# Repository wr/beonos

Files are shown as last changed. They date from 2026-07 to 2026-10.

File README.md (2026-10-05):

<p align="center">
  Beonos logo
</p>
<h1 align="center">Beonos Controller</h1>

<p align="center">
  <strong>Control your vintage Bang & Olufsen Beogram turntable from Home Assistant or Sonos.</strong>
</p>

<p align="center">
  <a href="#what-is-it">What is it?</a> ⬪
  <a href="#buy-a-board">Buy a board</a> ⬪
  <a href="#which-turntables">Which turntables</a> ⬪
  <a href="#hardware">Hardware</a> ⬪
  <a href="#firmware-esphome">Firmware</a> ⬪
  <a href="#repo-layout">Repo layout</a> ⬪
  <a href="#license">License</a>
</p>

<p align="center">
  <a href="https://youtu.be/ydfJdppEwTE">YouTube player</a>
</p>

<p align="center">
  I recorded a full build video that <a href="https://youtu.be/ydfJdppEwTE">you can watch here</a>.
</p>

---

## Buy a board

Get it as a kit, pre-soldered or not, from the [Wells Workshop shop](https://shop.wells.ee/products/beonos-kit/?ref=gh-beonos).

Or order your own Beonos Controller from [PCBway](https://www.pcbway.com/project/shareproject/Beonos_Controller_80184a3d.html). You can [use my referral code](https://pcbway.com/g/AsfKU9) to get $5 off your order, if you want. In my experience they're usually pretty fast and high quality, especially for the price.

## What is it?

A small ESP32-C6-powered custom PCB that splices into a Beogram's keyboard cable, reads what the turntable is doing, and sends play/pause/stop commands. The result is a 'smart' vintage turntable that behaves like a digital Sonos source.

- **Turntable → Sonos**: start the turntable and the speaker switches to Line-In and plays. Pause or switch off, and the speaker pauses.
- **Sonos → turntable**: pick Line-In on the speaker and the turntable starts (it presses Cue). Switch away or pause, and the turntable stops. If there's no record on the platter, the firmware notices and pauses Sonos rather than leaving it playing silence.

The board splices in-line, so nothing about the turntable is modified permanently — unplug the two headers and it's stock again.

## Which turntables

The Beogram 1800 family — the last generation of radial-arm Beograms — all share one control board, so the splice is the same across them:

| Model | Years | Status |
| ----- | ----- | --- |
| Beogram RX 2 | 1985–90 | Built and tested against this |
| Beogram 1800 | 1983–84 | Confirmed from service manuals |
| Beogram 2000 | 1983 | Confirmed from service manuals |
| Beogram 5000 | 1984 | Confirmed from service manuals |
| Beogram RX | 1984 | Very likely, not yet verified |

The RX-2 service manual is published as a supplement to the Beogram 1800/2000/5000 manual, and the three share the same power supply (PCB 8005076) and control board (PCB 8005117). Their keyboards are the same two sub-boards — 8005070 for PLAY/STOP and 8005109 for 45/CUE/33 — landing on the same P7 pins, which is what this board splices into. The RX is unverified only because no manual was to hand; it replaced the 1800 and differs from the RX 2 mainly in being supplied with a pickup.

**Not compatible.** The Beogram 2200 looks close but wires its speed switches straight to the control board alongside indicator lamps and a motor relay, with no separate keyboard board and no CUE or PLAY/STOP lines to intercept. Tangential-arm Beograms (4002, 8000, 6500, 7000, 9000, 5005 and relatives) use a different arm and control system entirely, and pre-1983 radial decks predate this microcomputer control.

To identify an unknown deck, look for a control PCB stamped **8005117**, a 24-pin MCU marked **B040680** / **ETL 5410N**, and a keyboard on its own cable whose buttons switch +12V.

## Hardware

- **MCU**: Seeed Studio XIAO ESP32-C6 (castellated edge-mount module)
- **Button drivers**: 2× LTV-356T optocouplers, switching the turntable's +12V onto the CUE and PLAYPAUSE lines exactly as the real buttons do
- **Level shifters**: 2× 1M/1.5M dividers dropping the COP410's 5.3V logic to ~3.18V for the ESP's 3.3V inputs. The values are deliberately high so the divider barely loads the COP410's weak CMOS outputs, and any overvoltage is current-limited into the ESP's ESD clamps.
- **Power**: an off-board MP1584EN buck module (PS1) steps the +12V button rail down to 5V, so the board draws everything from the button cable and never taps the 5.3V supply. The module hangs on flying leads; the board carries four wire pads for it.
- **Decoupling**: 10µF + 100nF on the buck's 5V output
- **Input filtering**: 10nF from each divider midpoint to ground, below R6/R8. The dividers present ~600kΩ to the ESP on wires that run past a motor; the caps give a ~6ms time constant, well inside the firmware's 50 ms debounce.
- **Connectors**: two 1×8 horizontal headers for the in-line splice — J1 (socket, silkscreened `TO BOARD`) and J2 (header, silkscreened `TO KEYBOARD`). Pins 1, 2, 4, 6, 7, 8 pass straight through; pins 3 and 5 also land on the optocoupler emitters.
- **Flying leads**: the two COP410 sense signals and a ground reference arrive on test pads (TP2, TP3, TP5); four more pads go out to the buck module. Everything is silkscreened by function — `On-Off IN`, `PlayPause IN`, `GND IN`, `12V`, `5V`, `GND` — so solder by the printed label, not the designator.

Board is 25 × 64 mm, two layers. Sources are `beogram-esp32.kicad_pcb` / `.kicad_sch` / `.kicad_pro`, with the BOM in [`bom.csv`](bom.csv).

### Pin map

| XIAO pin | Pad | GPIO | Net | Purpose |
| --- | --- | --- | --- | --- |
| D0 | 1 | GPIO0  | IN_OnOff_3V3 | COP410 pin 11 → ESP. LOW = arm in (turntable on) |
| D3 | 4 | GPIO21 | IN_PlayPause_3V3  | COP410 pin 12 → ESP. HIGH = playing |
| D8 | 9 | GPIO19 | DRV_PlayPause | ESP → U2 opto LED. Pulse 500 ms to "press" PLAYPAUSE |
| D10 | 11  | GPIO18 | DRV_Cue | ESP → U3 opto LED. Pulse 500 ms to "press" CUE |
| 5V | 14  | — | VCC | 5V in from the MP1584 buck (PS1) |
| GND | 13  | — | GND | Common ground |

D6/D7 (GPIO16/17) are UART0 and are left unconnected on purpose, so the ROM bootloader's serial output can't reach an optocoupler on reset.

## Firmware (ESPHome)

```bash
pip install esphome
cp secrets.yaml.example secrets.yaml
# fill in WiFi creds in secrets.yaml
esphome run beogram-rx2.yaml
```

First flash needs USB-C; after that, updates go over the air.

### Configuring the Sonos speaker

Once it joins WiFi the device shows up in Home Assistant. Set the **"Sonos IP"** entity to your speaker's address. That's the only setup — the RINCON UUID is discovered from the speaker on boot.

### Exposed entities

| Entity | Type | Notes |
| --- | --- | --- |
| Turntable On | binary_sensor  | true = arm in / playing position |
| Turntable Playing | binary_sensor  | true = motor on, arm down |
| Sonos Playing | binary_sensor  | derived from polled transport state |
| Sonos On Line-In | binary_sensor  | true if speaker is on line-in |
| Sonos Transport State | text_sensor | PLAYING / PAUSED_PLAYBACK / STOPPED |
| Sonos Current URI | text_sensor | what the speaker is currently playing |
| Sonos IP | text (config)  | edit in HA, persists across reboots |
| Press Play/Pause | button | manually fire the turntable's PLAYPAUSE |
| Press Cue | button | manually fire the turntable's CUE |
| Sonos Play / Pause | buttons | manual SOAP commands |
| Sonos Switch to Line-In | button | manual SOAP command |
| WiFi Signal | sensor | dBm, 60s update |

## Repo layout

```
beogram-esp32.kicad_pro     KiCad project
beogram-esp32.kicad_sch     Schematic
beogram-esp32.kicad_pcb     PCB layout
fp-lib-table                Registers the project footprint libraries
sym-lib-table               Registers the project symbol library
beogram.pretty/             Project footprints (MP1584 wire pads)
beogram.kicad_sym           Project symbols
New_XIAO_Series_Footprints/ Seeed's XIAO footprint library (vendor)
beogram-rx2.yaml            ESPHome firmware config
secrets.yaml.example        Template for WiFi/OTA/API creds
bom.csv                     Bill of materials
bang-olufsen_beogram_rx2_sch.pdf   RX 2 service-manual schematic, for reference
```

## Credits

ESPHome, the Seeed Studio XIAO ESP32-C6, KiCad, and Bang & Olufsen's engineers, who documented the RX2 well enough to reverse a splice point out of it forty years later.

## Donate

While beonos is free and open source, donations are deeply appreciated, and make ongoing development and support possible.
[Donate now](https://www.buymeacoffee.com/wellsworkshop)

## License

[CC BY-NC-SA 4.0](LICENSE). © 2026 Wells Riley.

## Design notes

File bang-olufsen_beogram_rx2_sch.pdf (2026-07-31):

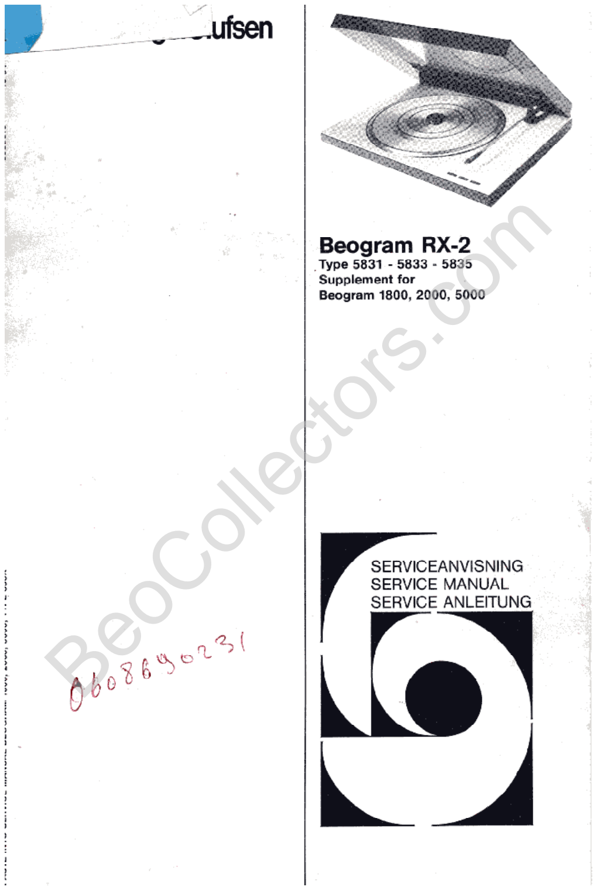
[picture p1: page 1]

BeoCollectors.

com

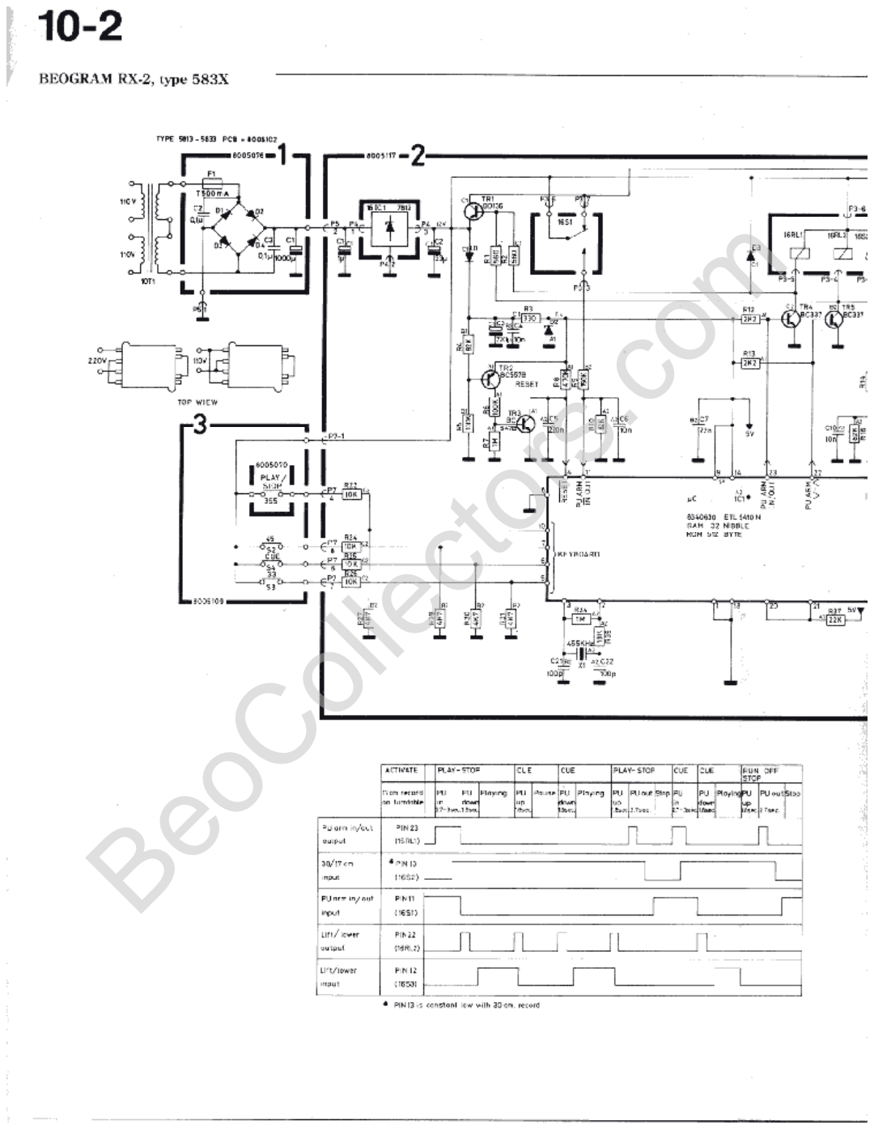
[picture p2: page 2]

BeoCollectors.

com

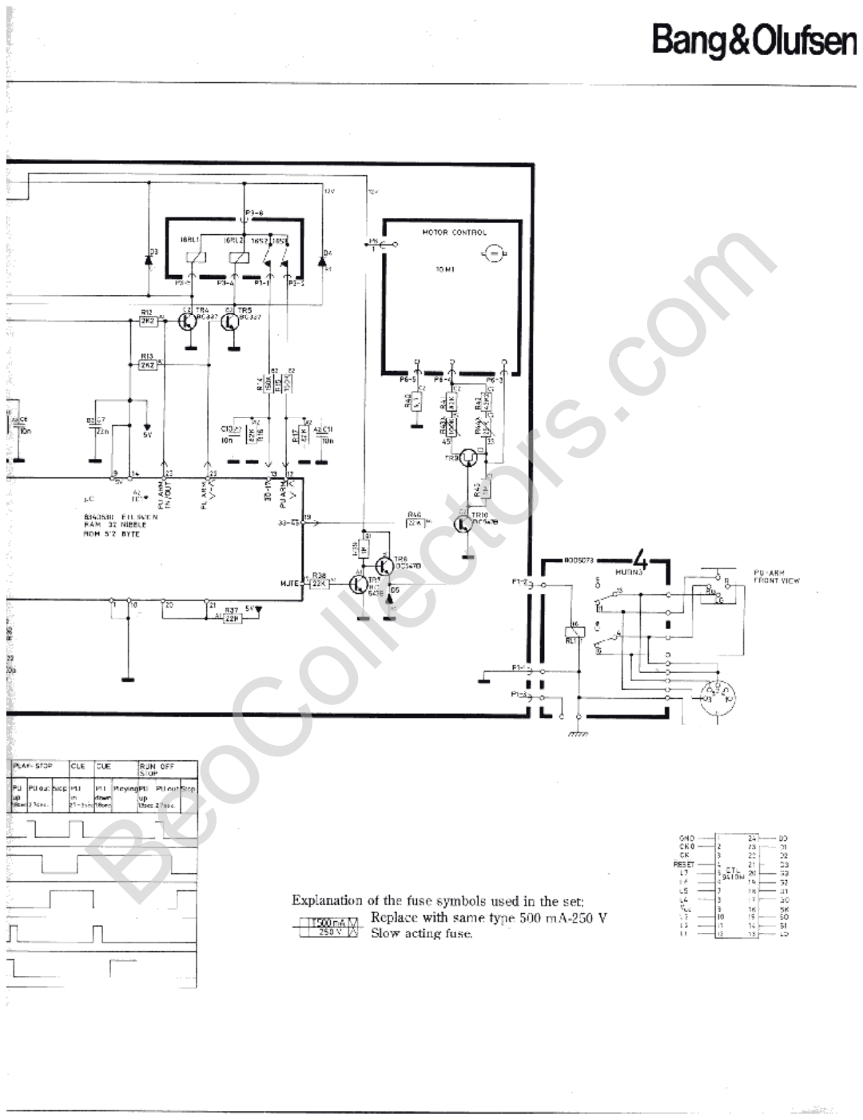
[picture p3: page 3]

BeoCollectors.

com

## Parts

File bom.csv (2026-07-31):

references | value | footprint | quantity
C2 | 100nF | Capacitor_SMD:C_0402_1005Metric | 1
C3,C4 | 10nF | Capacitor_SMD:C_0402_1005Metric | 2
C1 | 10uF | Capacitor_SMD:C_0402_1005Metric | 1
J2 | 2.54-1*40P right-angle(C2334) | Connector_PinHeader_2.54mm:PinHeader_1x08_P2.54mm_Horizontal | 1
J1 | PM254-1-08-W-8.5(C2897390) | Connector_PinSocket_2.54mm:PinSocket_1x08_P2.54mm_Horizontal | 1
U1 | SEEED STUDIO XIAO ESP32C6 | New_XIAO_Series_Footprints:XIAO-ESP32-C6-SMD | 1
U2,U3 | LTV-356T | Package_SO:SO-4_4.4x3.6mm_P2.54mm | 2
R6,R8 | 1.5M | Resistor_SMD:R_0402_1005Metric | 2
R5,R7 | 1M | Resistor_SMD:R_0402_1005Metric | 2
R1,R2 | 470R | Resistor_SMD:R_0402_1005Metric | 2
PS1 | MP1584EN module | beogram:MP1584_Module_Wired | 1

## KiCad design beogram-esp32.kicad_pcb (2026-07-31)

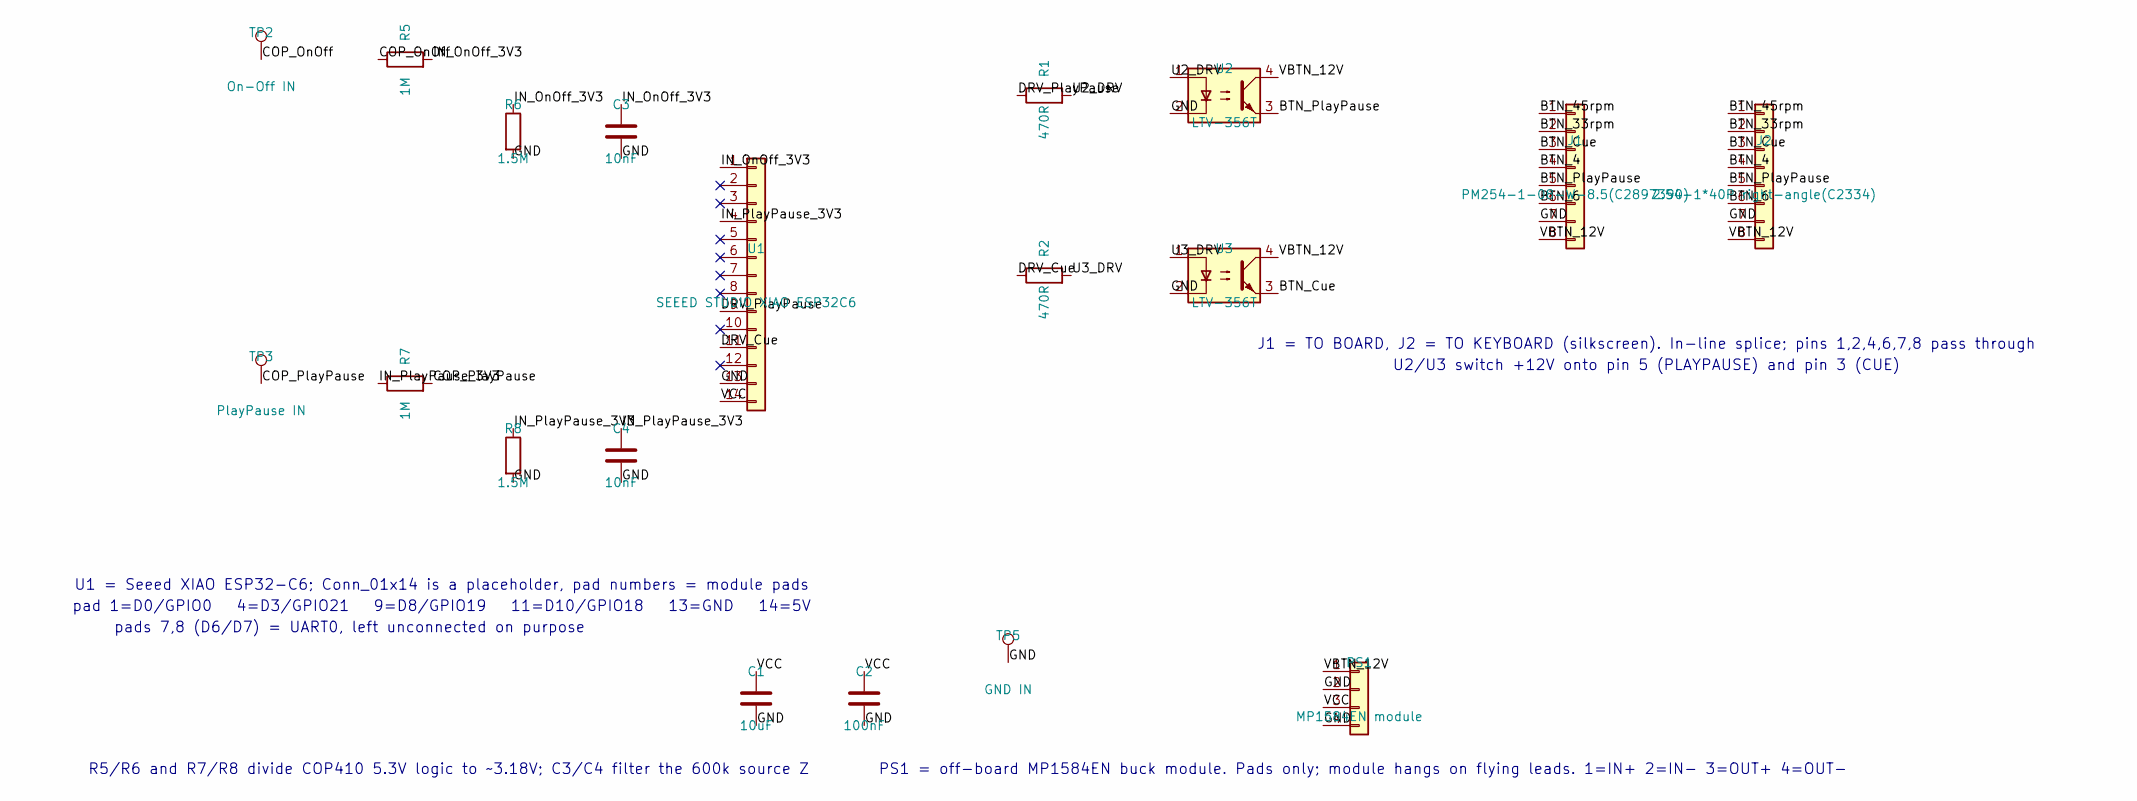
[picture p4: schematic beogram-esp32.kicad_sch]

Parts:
C1: 10uF; C_0402_1005Metric
C2: 100nF; C_0402_1005Metric
C3, C4: 10nF; C_0402_1005Metric
J1: PM254-1-08-W-8.5(C2897390); PinSocket_1x08_P2.54mm_Horizontal
J2: 2.54-1*40P right-angle(C2334); PinHeader_1x08_P2.54mm_Horizontal
PS1: MP1584EN module; MP1584_Module_Wired
R1, R2: 470R; R_0402_1005Metric
R5, R7: 1M; R_0402_1005Metric
R6, R8: 1.5M; R_0402_1005Metric
TP2: On-Off IN; TestPoint_Pad_1.5x1.5mm
TP3: PlayPause IN; TestPoint_Pad_1.5x1.5mm
TP5: GND IN; TestPoint_Pad_1.5x1.5mm
U1: SEEED STUDIO XIAO ESP32C6; XIAO-ESP32-C6-SMD
U2, U3: LTV-356T; SO-4_4.4x3.6mm_P2.54mm

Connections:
BTN_4: J1.4, J2.4
BTN_6: J1.6, J2.6
BTN_33rpm: J1.2, J2.2
BTN_45rpm: J1.1, J2.1
BTN_Cue: J1.3, J2.3, U3.3
BTN_PlayPause: J1.5, J2.5, U2.3
COP_OnOff: R5.1, TP2.1
COP_PlayPause: R7.2, TP3.1
DRV_Cue: R2.1, U1.11
DRV_PlayPause: R1.1, U1.9
GND: C1.2, C2.1, C3.1, C4.2, J1.7, J2.7, PS1.2, PS1.4, R6.2, R8.2, TP5.1, U1.13, U2.2, U3.2
IN_OnOff_3V3: C3.2, R5.2, R6.1, U1.1
IN_PlayPause_3V3: C4.1, R7.1, R8.1, U1.4
U2_DRV: R1.2, U2.1
U3_DRV: R2.2, U3.1
VBTN_12V: J1.8, J2.8, PS1.1, U2.4, U3.4
VCC: C1.1, C2.2, PS1.3, U1.14

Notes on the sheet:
U1 = Seeed XIAO ESP32-C6; Conn_01x14 is a placeholder, pad numbers = module pads
pad 1=D0/GPIO0 4=D3/GPIO21 9=D8/GPIO19 11=D10/GPIO18 13=GND 14=5V
pads 7,8 (D6/D7) = UART0, left unconnected on purpose
R5/R6 and R7/R8 divide COP410 5.3V logic to ~3.18V; C3/C4 filter the 600k source Z
U2/U3 switch +12V onto pin 5 (PLAYPAUSE) and pin 3 (CUE)
PS1 = off-board MP1584EN buck module. Pads only; module hangs on flying leads. 1=IN+ 2=IN- 3=OUT+ 4=OUT-
J1 = TO BOARD, J2 = TO KEYBOARD (silkscreen). In-line splice; pins 1,2,4,6,7,8 pass through

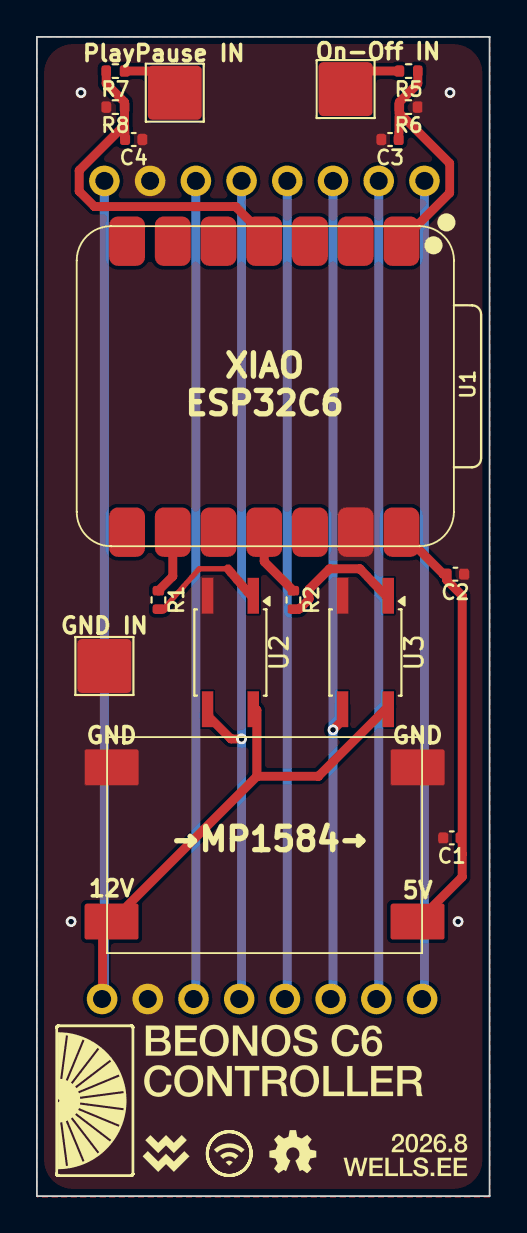
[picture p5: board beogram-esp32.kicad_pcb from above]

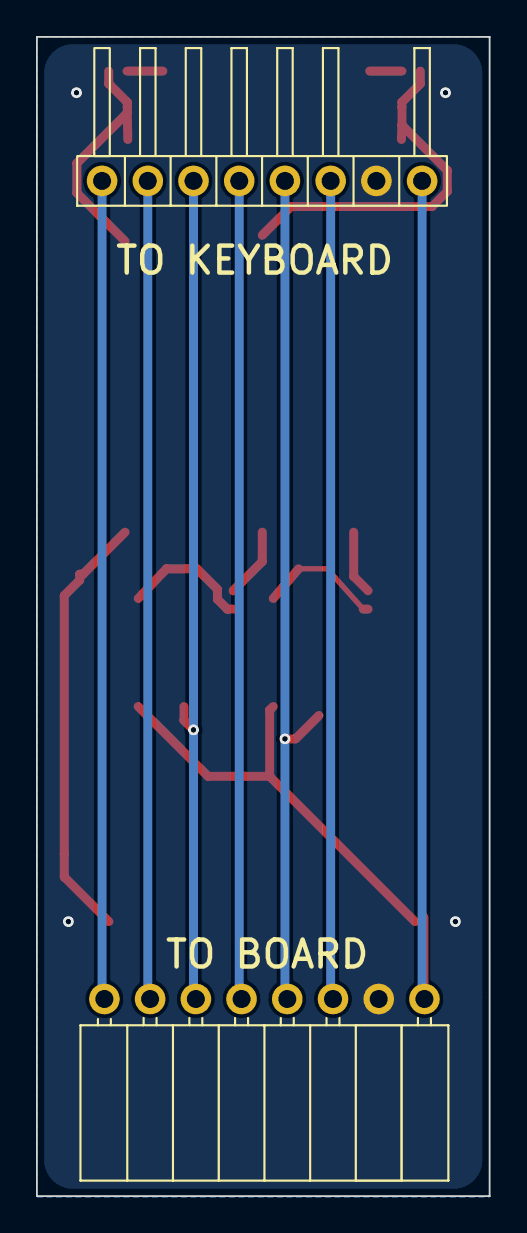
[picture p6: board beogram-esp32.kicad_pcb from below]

Board: 2 copper layers, 25.2 x 64.4 mm, 19 parts (2 on the bottom side), 17 nets.

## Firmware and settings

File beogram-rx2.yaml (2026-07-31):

# Beogram RX2 → Sonos bridge, ESP32-C6 (Seeed XIAO)
#
# Pin map (matches the PCB):
#   GPIO0  (D0)  — IN_OnOff_3V3      input from COP410 pin 11 via 1M/1.5M divider
#                                    COP410: LOW = arm-in (turntable ON), HIGH = arm-out (OFF)
#                                    We invert so the sensor reads true when the turntable is on.
#   GPIO21 (D3)  — IN_PlayPause_3V3  input from COP410 pin 12 via 1M/1.5M divider
#                                    COP410: HIGH = playing, LOW = paused/cued
#   GPIO19 (D8)  — DRV_PlayPause     drives U2 optocoupler LED; pulse HIGH 500ms
#                                    to switch +12V onto the PLAYPAUSE button line
#   GPIO18 (D10) — DRV_Cue           drives U3 optocoupler LED; pulse HIGH 500ms
#                                    to switch +12V onto the CUE button line
#
# All Sonos logic runs on the ESP — it talks UPnP/SOAP to the speaker directly.
# State is also exposed over the HA API so you can see what's happening and
# trigger manual button presses from Home Assistant.

substitutions:
  device_name: beogram-rx2
  friendly_name: Beogram RX2
  # How long to wait after pressing Cue before deciding "no record present".
  no_record_timeout: "6s"
  # Optocoupler drive pulse — long enough for the turntable's IC to register.
  press_pulse: "500ms"
  # Sonos IP is configurable from Home Assistant — see the `text:` block.
  # The RINCON UUID is auto-discovered from the speaker on boot.
  default_sonos_ip: "10.0.1.154"

esphome:
  name: ${device_name}
  friendly_name: ${friendly_name}
  on_boot:
    priority: 250
    then:
      # Wait for inputs to settle before bridge logic kicks in, so we don't
      # mistake startup transients for state changes.
      - delay: 3s
      - globals.set:
          id: system_ready
          value: "true"
      - logger.log: "System ready — bridge logic active"
      # Pull the speaker's RINCON UUID from its UPnP device description.
      - script.execute: discover_rincon

esp32:
  board: seeed_xiao_esp32c6
  framework:
    type: esp-idf
    sdkconfig_options:
      CONFIG_ESP_CONSOLE_USB_SERIAL_JTAG: "y"
      CONFIG_ESP_CONSOLE_SECONDARY_NONE: "y"

logger:
  level: INFO

api:
  encryption:
    key: !secret api_encryption_key

ota:
  - platform: esphome

wifi:
  ssid: !secret wifi_ssid_1
  password: !secret wifi_password_1
#  ap:
#    ssid: "${friendly_name} Fallback"
#    password: !secret wifi_captive

http_request:
  useragent: esphome/${device_name}
  timeout: 4s

# ── Globals ─────────────────────────────────────────────────────────────────

globals:
  - id: system_ready
    type: bool
    initial_value: "false"
  - id: prev_turntable_on
    type: bool
    initial_value: "false"
  - id: prev_turntable_playing
    type: bool
    initial_value: "false"
  - id: prev_sonos_line_in
    type: bool
    initial_value: "false"
  - id: prev_sonos_playing
    type: bool
    initial_value: "false"

# ── Inputs from the turntable ───────────────────────────────────────────────

binary_sensor:
  - platform: gpio
    name: "Turntable On"
    id: turntable_on
    pin:
      number: GPIO0
      mode:
        input: true
      inverted: true   # COP410 pin 11 is LOW when arm is in (playing position)
    filters:
      - delayed_on: 50ms
      - delayed_off: 50ms
    on_state:
      then:
        - script.execute: react_to_turntable

  - platform: gpio
    name: "Turntable Playing"
    id: turntable_playing
    pin:
      number: GPIO21
      mode:
        input: true
    filters:
      - delayed_on: 50ms
      - delayed_off: 50ms
    on_state:
      then:
        - script.execute: react_to_turntable

  # Derived from Sonos polling — published for visibility in HA.
  - platform: template
    name: "Sonos Playing"
    id: sonos_playing
    lambda: |-
      return id(sonos_transport).state == "PLAYING";
    on_state:
      then:
        - script.execute: react_to_sonos

  - platform: template
    name: "Sonos On Line-In"
    id: sonos_line_in
    lambda: |-
      // Line-in URI is "x-rincon-stream:RINCON_xxx"; we just check the prefix.
      return id(sonos_uri).state.find("x-rincon-stream:") == 0;
    on_state:
      then:
        - script.execute: react_to_sonos

# ── Outputs to the optocoupler drivers ──────────────────────────────────────

output:
  - platform: gpio
    pin: GPIO19
    id: drv_playpause
  - platform: gpio
    pin: GPIO18
    id: drv_cue

# ── Buttons exposed to HA (and used internally) ─────────────────────────────

button:
  - platform: template
    name: "Press Play-Pause"
    on_press:
      - script.execute: pulse_playpause

  - platform: template
    name: "Press Cue"
    on_press:
      - script.execute: pulse_cue

  - platform: template
    name: "Sonos Play"
    on_press:
      - script.execute: sonos_play
  - platform: template
    name: "Sonos Pause"
    on_press:
      - script.execute: sonos_pause
  - platform: template
    name: "Sonos Switch to Line-In"
    on_press:
      - script.execute: sonos_switch_to_line_in
  - platform: template
    name: "Rediscover Sonos RINCON"
    entity_category: config
    on_press:
      - script.execute: discover_rincon

# ── Sonos state (populated by the polling interval) ────────────────────────

text_sensor:
  - platform: template
    name: "Sonos Transport State"
    id: sonos_transport
    update_interval: never
  - platform: template
    name: "Sonos Current URI"
    id: sonos_uri
    update_interval: never
  # Auto-discovered from the speaker's UPnP device description on boot.
  - platform: template
    name: "Sonos RINCON UUID"
    id: sonos_rincon
    update_interval: never
    entity_category: diagnostic

sensor:
  - platform: wifi_signal
    name: "WiFi Signal"
    update_interval: 60s

# ── Sonos device config (editable in HA, persists across reboots) ──────────

text:
  - platform: template
    name: "Sonos IP"
    id: sonos_ip
    optimistic: true
    restore_value: true
    initial_value: "${default_sonos_ip}"
    min_length: 7
    max_length: 15
    mode: text
    entity_category: config
    on_value:
      then:
        # Re-discover when the IP changes
        - script.execute: discover_rincon

# ── Scripts ─────────────────────────────────────────────────────────────────
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

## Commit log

2026-05-13 Align PCB component references with schematic
    [beogram-esp32.kicad_pcb]
2026-05-14 Board layout update
    [beogram-esp32.kicad_pcb]
2026-05-14 Fix compile errors: avoid raw string in lambda, rename button
    [beogram-rx2.yaml]
